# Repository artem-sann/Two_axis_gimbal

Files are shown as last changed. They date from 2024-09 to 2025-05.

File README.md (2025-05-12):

# 📦 Разработка двухосевого подвеса направленной антнны для установки на БПЛА

**Краткое описание:**  
Для достижения значительного увеличения дальности разрабатывается система ретрансляции управляющего сигнала и видеосигнала. Предполагается, что использование дополнительного БПЛА между оператором и FPV летательным аппаратом увеличит дальность полета, при этом уделяется внимание использованию направленных антенн, и их позиционирование при помощи следящего привода, используя как входные данные уровень сигнала - RSSI (Received Signal Strength Indicator). Концепт системы на рис. 1.

<p align="center">
  
</p>

---

## 📁 Структура проекта

```
Two_axis_gimbal/
│
├── 3D_модели/                    # 3D-модели и детали (Inventor)
│   ├── Вспомогательные модели/   # Сборка для предварительных расчетов (Inventor)             
│   ├── Основная сборка/          # Основная сборка
│   └── Испытательный стенд/      # Сборка испытательного стенда
│
├── Dual_BLDC_Controller/         # Проект печатной платы блока управления (Altium)
│   └── Library                   # Собственная библиотека компонентов
│
├── MATLAB_part/                  # Мат. моделирование и синтез корректирующего устройства
│   └── scripts
│       └── Read_COM              # Скрипт для считывания показаний устройства через COM-порт
├── Python/                       # Скрипты визуализации алгоритмов управления
│   └── ...            
│
├── STM32/                        # ПО для микроконтроллера STM32F401
│   └── ...
│
├── Функциональные и кинематические схемы и тд/               
│   └── ...
│
├── Документация/                 # Все НИРы КП и КР и прочая текстовая документация
│   └── ...
│
├── LICENSE               # Лицензия проекта
├── README.md             # Документация первого уровня (этот файл)
└── .gitignore
```

---

## 🛠️ Используемые технологии

- **MCU:** STM32F401
- **CAD:** Компас / SolidWorks / Inventor
- **Программирование:** C, Python, Matlab, Simulink 
- **Протоколы связи и технологии:** UART, SPI, DMA, ADC, PWM
- **Среда разработки:** STM32CubeIDE, VS Code, Matlab
---

## 🖼️ Превью проекта

> Реализованный прототип для тестирования и отработки основного функционала:
<p align="center">
  
</p>

---

## 📃 Документация

Подробная информация доступна в папке `Документация/`. Включает:

- 2 НИРа с общим описанием системы
- КП по ТАУ с описанием системы управления
- КП по Электронике с описанием платы управления
- Календарные планы
- КП по экономике

---

## 🔧 Сборка и запуск

1. **Сборка аппаратной части**  
   Ознакомьтесь с файлами в `3D_модели/`. В ней расположен Inventor проект с подробной 3Д моделью.

2. **Прошивка микроконтроллера**  
   Перейдите в папку `STM32/`, откройте проект в [PlatformIO / STM32CubeIDE] и прошейте контроллер.

---

## 🧪 Тестирование

Результаты тестирования представлены в файле НИР2_оформленный.docx

<p align="center">
  
  
</p>

---

## 🤝 Участие

Если вы хотите внести вклад:

1. Сделайте форк проекта
2. Создайте ветку для своей функции (`git checkout -b feature/YourFeature`)
3. Сделайте коммит (`git commit -m 'Add some feature'`)
4. Отправьте пул-реквест

---

## 📬 Контакты

- Автор: [Артём Санников]
- Email: [artemksannikov@gmail.com]
- Telegram: [@artem_sann]

---

## 📌 TODO

- [ ] Привести код для STM32 в порядок
- [ ] Переработать печатную плату с учетом правок
- [ ] Опубликовать где нибудь

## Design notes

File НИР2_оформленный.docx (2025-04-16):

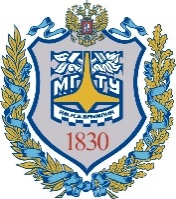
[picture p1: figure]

| Министерство науки и высшего образования Российской Федерации Федеральное государственное бюджетное образовательное учреждение высшего образования «Московский государственный технический университет имени Н.Э. Баумана (национальный исследовательский университет)» (МГТУ им. Н.Э. Баумана)

ФАКУЛЬТЕТ «Специальное машиностроение»

КАФЕДРА «Робототехнические системы и мехатроника»

РАСЧЕТНО-ПОЯСНИТЕЛЬНАЯ ЗАПИСКА

К НАУЧНО-ИССЛЕДОВАТЕЛЬСКОЙ РАБОТЕ

НА ТЕМУ:

Разработка двухосевого привода направленной антенны для установки на БПЛА

Студент СМ7-82Б _________________ Санников А.К.

(Группа) (Подпись, дата) (И.О.Фамилия)

Руководитель _________________ Гуляев И.А.

(Подпись, дата) (И.О.Фамилия)

Консультант _________________ ____________________

(Подпись, дата) (И.О.Фамилия)

2025 г.

Министерство науки и высшего образования Российской Федерации

Федеральное государственное бюджетное образовательное учреждение

высшего образования

«Московский государственный технический университет имени Н.Э. Баумана

(национальный исследовательский университет)»

(МГТУ им. Н.Э. Баумана)

УТВЕРЖДАЮ

Заведующий кафедрой __________

(Индекс)

______________ _______________

(И.О.Фамилия)

« _____ » ____________ 20 ____ г.

ЗАДАНИЕ

на выполнение научно-исследовательской работы

По теме: | Разработка двухосевого привода направленной антенны

для установки на БПЛА

Студент группы ____СМ7-82б___________

_________________________Санников Артём Константинович__________________________

(Фамилия, имя, отчество)

Направленность НИР (учебная, исследовательская, практическая, производственная, др.)

________практическая____________________________________________________________

Источник тематики (кафедра, предприятие, НИР) _____________________________________

График выполнения НИР: 25% к 5 нед., 50% к 7 нед., 75% к 10 нед., 100% к 12 нед.

Техническое задание | Разработать двухосевой привод для встраивания в систему

ретрансляции сигнала с возможностью установки на БПЛА для увеличения дальности

передачи сигнала

Оформление научно-исследовательской работы:

Расчетно-пояснительная записка на _____ листах формата А4.

Перечень графического (иллюстративного) материала (чертежи, плакаты, слайды и т.п.)

_______________________________________________________________________________

_______________________________________________________________________________

_______________________________________________________________________________

Дата выдачи задания « 17 » февраля 2025 г.

Руководитель НИР _________________ Гуляев И.А.

(Подпись, дата) (И.О.Фамилия)

Студент _________________ Санников А.К.

(Подпись, дата) (И.О.Фамилия)

Примечание: Задание оформляется в двух экземплярах: один выдается студенту, второй хранится на кафедре.

# РЕФЕРАТ

Расчетно-пояснительная записка 27 с. 17 рис., 3 табл., 8 источников.

ДВУХОСЕВОЙ ПРИВОД, БПЛА, НАПРАВЛЕННЫЕ АНТЕННЫ, РЕТРАНСЛЯТОР, РАЗРАБОТКА ПРИВОДА, РАЗРАБОТКА ПРОТОТИПА.

Объектом разработки является двухосевой привод направленной антенны.

Цель работы – разработка части системы ретрансляции сигнала для установки на БПЛА для увеличения дальности передачи сигнала, в частности прототип и испытательный стенд, а также систему управления.

Поставленная цель достигается за счет разработки двухосевого привода, направляющего антенну ретранслятора с необходимой точностью и с необходимым быстродействием, и установки данной системы на дополнительный БПЛА.

СОДЕРЖАНИЕ

# ВВЕДЕНИЕ

В настоящее время все чаще используются беспилотные летательные аппараты с FPV системами, как в исследовательских и разведывательных целях, так и в боевых условиях. Всё чаще возникает потребность в увеличении дальности работы, но при этом остается условие сохранять высокие скорости передачи данных. Решение задачи увеличения дальности передачи сигнала возможно за счёт установки ретранслятора с усилителем и на управляемом подвесе на вспомогательный БПЛА.

# 1 ОПИСАНИЕ СИСТЕМЫ И ПОСТАНОВКА ЗАДАЧИ

Для достижения значительного увеличения дальности разрабатывается система ретрансляции управляющего сигнала и видеосигнала. Предполагается, что использование дополнительного БПЛА между оператором и FPV летательным аппаратом увеличит дальность полета, при этом уделяется внимание использованию направленных антенн, и их позиционирование при помощи следящего привода, используя как входные данные уровень сигнала - RSSI (Received Signal Strength Indicator). Концепт системы на рис. 1.

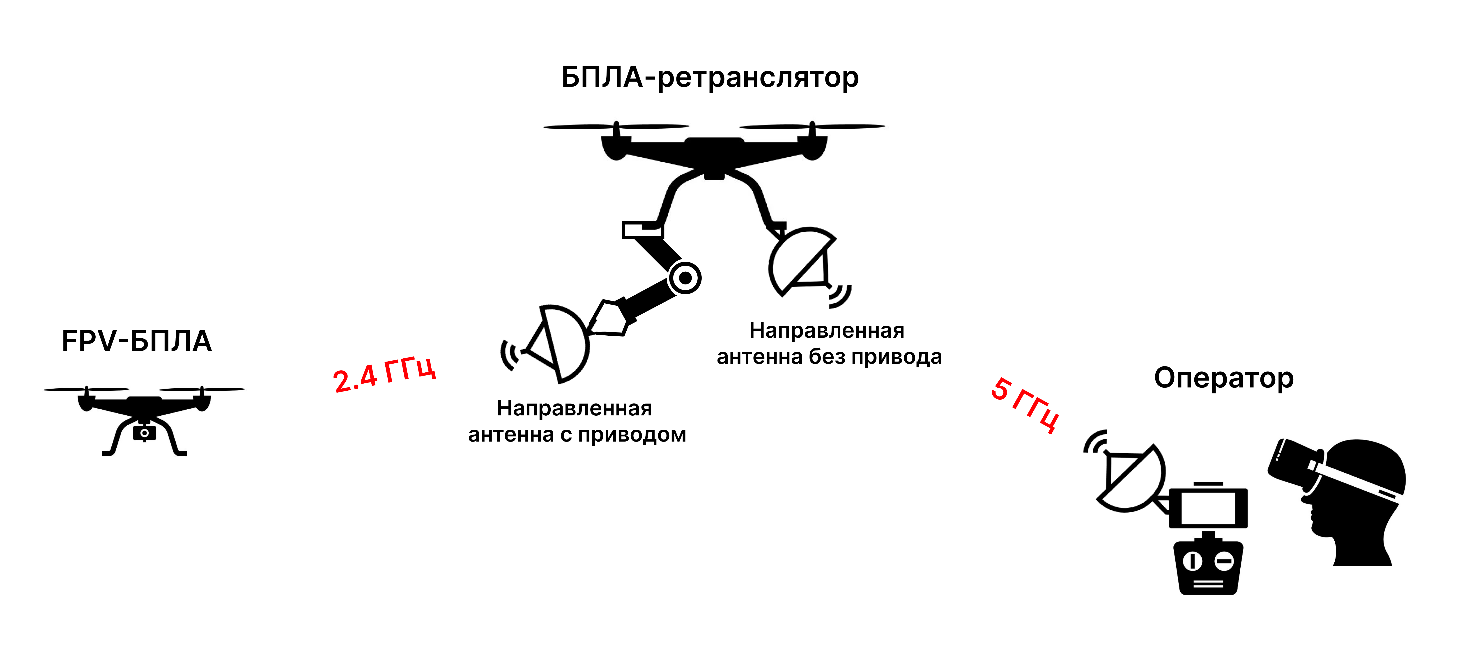
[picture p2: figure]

Рис. 1 Концепт системы ретрансляции

При этом на дрон ретранслятор устанавливается 2 антенны, одна из которых остается неподвижной и направляется при помощи поворота дрона, а вторая устанавливается на двухосевой привод, который в свою очередь направляет антенну на FPV-дрон.

В рамках данного проекта ставится техническое задание на разработку только части системы – двухосевого привода антенны, и выбор компонетов системы: антенн и тд.

# 2 КОНСТРУКЦИЯ РАЗРАБАТЫВАЕМОГО ИЗДЕЛИЯ

Разрабатываемое устройство представляет из себя – подвесной модуль для мультикоптерных
Здесь кинематическая схема

## 2.1 Разработка прототипа

Данная система позволяет увеличивать дальность полетов, что будет очень полезно для применения в боевых условиях, а также для разведывательных и исследовательских целей, везде где требуется большая дальность и сохранение FPV функций.

## 2.2 Разработка испытательного стенда

Существуют двухосевые подвесы-стабилизаторы для аэрофотосъемки, также существуют дроны-ретрансляторы с двумя неподвижными антеннами широкой направленности. По сути новизна заключается в объединении этих двух идей, с целью увеличения дальности полета и повышении эффективности ретрансляции.

Основная актуальность работы – применение в боевых условиях. Так как в таких условиях наиболее важна дальность передачи сигнала.

# 3 ИЗГОТОВЛЕНИЕ И СБОРКА ПРОТОТИПА И ИСПЫТАНИЯ

## 3.1 Изготовление деталей

Рассматривая аналоги привода можно рассмотреть как косвенные аналоги – подвесы-

## 3.2 Сборка и подключение стенда

По контекстным запросам:

- «Разработка двухосевого привода направленной антенны для установки на БПЛА»
- «two-axis drive of directional antenna for UAV. UAV is equipped with device with 2-axis drive and directional antenna, using stepper motors directs antenna.»,
- « двухосевой привод направленной антенны для бпла с для увеличения дальности полетов на бпла устанавливается устройство с 2 осевым приводом, и направленной антенной, с помощью шаговых двигателей направляет антенну.»

Отсутствуют релевантные результаты.

## 3.3 Реализация корректирующего устройства на МК и испытания

# 4 ОПРЕДЕЛЕНИЕ ПРИГОДНЫХ ТИПОВ И РАЗМЕРОВ БПЛА

грузоподъемности представлена в таблице 1:

Таблица 1. Сравнение типов и размеров БПЛА

Типоразмер БПЛА | Масса | Грузо-сть | Габариты в диаметр | Время полета | Макс.Высота полета
Микро-класс | До 50 гр. | 10 гр. | До 100 мм | 3-10 мин. | 10 м
Мини-класс | До 500 гр. | 100 гр. | До 250 мм. | 5-20 мин. | 100 м
Средний класс | До 2.5 кг. | 500 гр. | 350-500 мм | 30 мин. | 1000 м
Тяжелый класс | От 2.5 кг. | От 1 кг. | От 550 мм | От 50 мин. | От 1000 м

Для прототипа предприятием заказчиком был выбран квадрокоптер тяжелого класса: DJI MATRICE 300, его характеристики можно брать за основу при проектировании привода, внешний вид представлен на рис. 5.

# 4 УРАВНЕНИЯ ДВИЖЕНИЯ И РАСЧЕТ РАБОЧЕЙ ОБЛАСТИ УСТРОЙСТВА

Для определения структуры устройства создадим функциональную схему. В данной научно-исследовательской работе рассматривается разработка одной из частей системы – часть на рис. 6 начиная с микроконтроллера и ниже.

Рис. 6 Функциональная схема устройства

# ЗАКЛЮЧЕНИЕ

В заключение работы, обобщим краткое техническое задание на разработку двухосевого привода.

# СПИСОК ИСПОЛЬЗОВАННЫХ ИСТОЧНИКОВ

1) Ротхаммель К. Энциклопедия антенн: Antennenbuch под ред. Кришке А. Изд. 11-е: Издательство ДМК-Пресс 2016. 812с. ISBN 978-5-97060-217-1

2) Биард Рэндал У., МакЛэйн Тимоти У. Малые беспилотные летательные аппараты: теория и практика 2012. 309 с.

3) C.В. Овсянников, А.А. Бошляков, А.О. Кузьмина ЭКСПЕРИМЕНТАЛЬНЫЕ ИССЛЕДОВАНИЯ В МЕХАТРОННЫХ СИСТЕМАХ

4) DJI LLC Краткое руководство пользователя DJI MATRICE 300 2015. 109 с.

5) Кокорев Ю.А., Жаров В.А., Торгов А.М. Расчет электромеханического привода: Учеб. пособие Под ред. В.Н.Баранова. — М.: Изд-во МГТУ, І995. 132 с

6) А.И. Еремеев и др.; Под. ред. О.Ф. Тищенко. А 1. тлас конструкций элементов приборных устройств: Учеб. Пособие для студентов приборостроительных специальностей ВУЗов /А.А. Буцев, М.: Машиностроение, 1982. 116с.

7) М. Г. Алешин, С. В. Дьяконов, А. Ю. Сивов, ОБОСНОВАНИЕ ОСНОВНЫХ ХАРАКТЕРИСТИК АНТЕННОЙ СИСТЕМЫ И ПАРАМЕТРОВ УПРАВЛЕНИЯ МОЩНОСТЬЮ ПЕРЕДАТЧИКА РЕТРАНСЛЯТОРА СВЯЗИ НА БЕСПИЛОТНОМ ЛЕТАТЕЛЬНОМ АППАРАТЕ 2011. 21 c.

8) К.О. Коровин , С.В. Кузьмин, Реализация канала связи с БПЛА с использованием широкополосных малоэлементных антенных решеток в качестве бортовых антенных систем, 2020, 6 с.

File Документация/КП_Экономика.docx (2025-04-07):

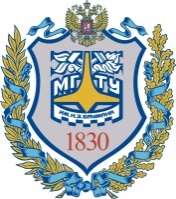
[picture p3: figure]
Gerb-BMSTU_01

| Министерство образования и науки Российской Федерации Федеральное государственное бюджетное образовательное учреждение высшего образования «Московский государственный технический университет имени Н.Э. Баумана (национальный исследовательский университет)» (МГТУ им. Н.Э. Баумана)

ФАКУЛЬТЕТ ИНЖЕНЕРНЫЙ БИЗНЕС И МЕНЕДЖМЕНТ

КАФЕДРА ЭКОНОМИКА И ОРГАНИЗАЦИЯ ПРОИЗВОДСТВА

РАСЧЕТНО-ПОЯСНИТЕЛЬНАЯ ЗАПИСКА

К КУРСОВОЙ РАБОТЕ ПО КУРСУ

ЭКОНОМИКА ПРЕДПРИЯТИЯ

НА ТЕМУ:

Организация и планирование

проведения НИОКР по теме

«Разработка двухосевого _

_ привода направленной антенны ___ _ _ для установки на БПЛА» __

Студент ____СМ7-82Б__ _________________ _Санников А .К__

(Группа) (Подпись, дата) (И.О.Фамилия)

Руководитель курсовой работы _________________ ___А.В.Волохов _

(Подпись, дата) (И.О.Фамилия)

Москва 2025 г.

# 1. Введение

В настоящее время все чаще используются беспилотные летательные аппараты с FPV системами, как в исследовательских и разведывательных целях, так и в боевых условиях. Всё чаще возникает потребность в увеличении дальности работы, но при этом остается условие сохранять высокие скорости передачи данных. Решение задачи увеличения дальности передачи сигнала возможно за счёт установки ретранслятора с усилителем и на управляемом подвесе на вспомогательный БПЛА.

Для достижения значительного увеличения дальности разрабатывается система ретрансляции управляющего сигнала и видеосигнала. Предполагается, что использование дополнительного БПЛА между оператором и FPV летательным аппаратом увеличит дальность полета, при этом уделяется внимание использованию направленных антенн, и их позиционирование при помощи следящего привода, используя как входные данные уровень сигнала - RSSI (Received Signal Strength Indicator). Концепт системы на рис. 1.


Рис. 1 Концепт системы ретрансляции

При этом на дрон ретранслятор устанавливается 2 антенны, одна из которых остается неподвижной и направляется при помощи поворота дрона, а вторая устанавливается на двухосевой привод, который в свою очередь направляет антенну на FPV-дрон.

Для этого необходимо разработать систему управления приводом (рис. 2) и отдельную плату, для управления электроприводами (рис. 3).

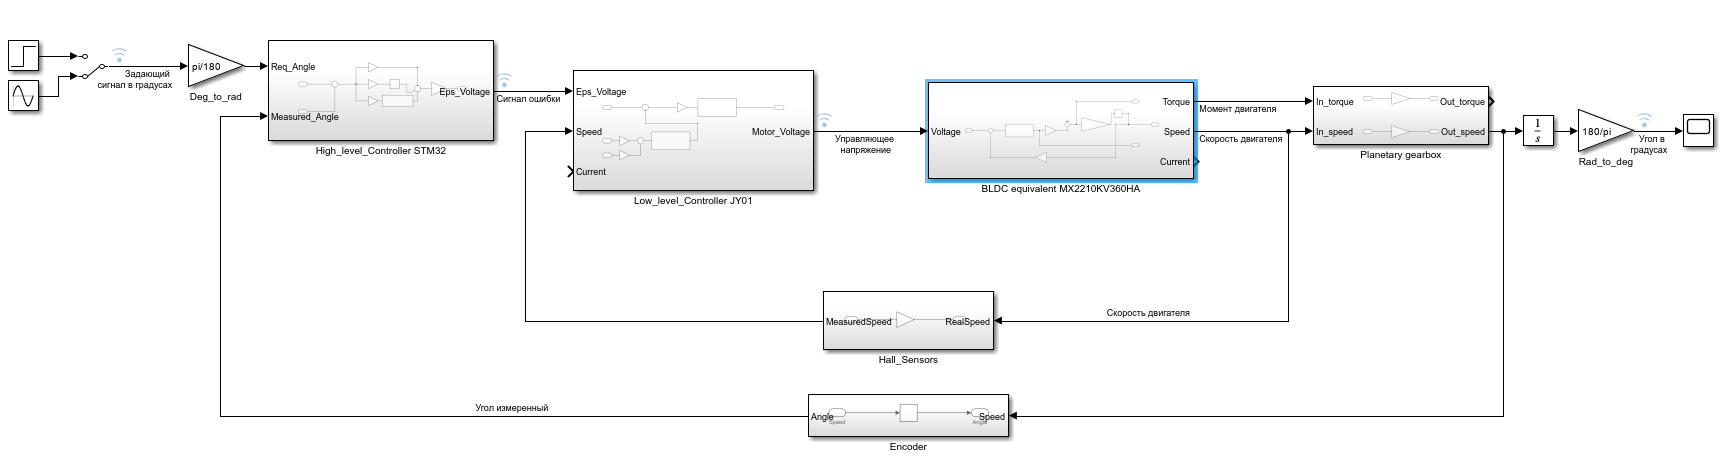
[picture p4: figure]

Рис. 2– система управления приводом

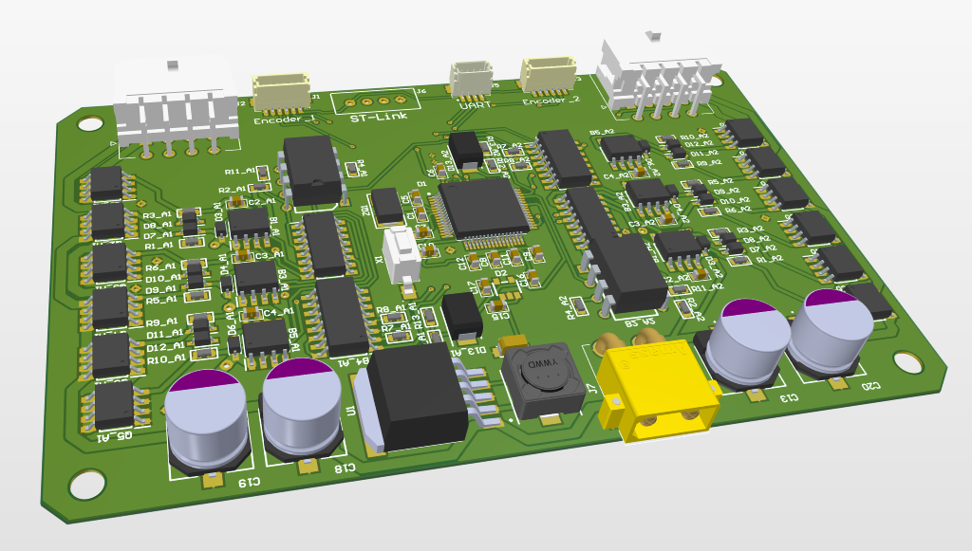
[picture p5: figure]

Рис. 3– плата системы управления приводом

В рамках данной курсовой работы будет рассмотрена организация научно-исследовательской и опытно-конструкторской работы. Для этого необходимо:

1. Разбить проект на отдельные части.
2. Определить длительность каждого этапа проектирования и производства.
3. Выбрать необходимое оборудование и работников для производства изделия.
4. Далее, после проведения всех расчетов, произвести оценку технической и экономической составляющих НИОКР.
5. Проанализировать все составляющие и сделать вывод о возможности производства данного изделия.

# 2. Основная часть

Составим дифференциальный перечень работ по всем этапам НИОКР с учётом их специфики:

Перечень этапов НИР:

- разработка технического задания на НИР;
- выбор направления исследования;
- подготовка экспериментальной базы;
- теоретические и экспериментальные исследования;
- обобщение и оценка результатов исследований;

Перечень этапов ОКР:

- разработка технического задания на ОКР;
- разработка технического предложения;
- эскизное проектирование;
- техническое проектирование;
- разработка рабочего проекта и оформление технической документации;
- изготовление опытного образца;
- испытания опытного образца;
- доработка проекта по результатам испытаний.

## 2.1. Определение сроков проведения НИОКР с составлением план-графика

Для определения сроков проведения НИОКР используем вероятностную методику определения продолжительности проведения работ на основе двухточечной оценки трудоёмкости:

T_(ож i) =(3T_(mini) +2T_(maxi))/5

Где:

T_(ож i) - ожидаемая продолжительность проведения работ;

T_(mini) – минимальная продолжительность проведения работы;

T_(maxi) – максимальная продолжительность проведения работы.

T_i =(τ_i k_(р-к))/(R_i F_(пл) K_(вн))

Где:

T_i – продолжительность проведения работы i при использовании трудоёмкости;

τ_i – трудоёмкость работы i (чел.-дн.);

k_(р-к) =1,45 – коэффициент перевода рабочих дней в календарные (если F_(пл) задан в календарных днях за период);

R_i – число исполнителей работы i, чел.;

F_(пл) – плановый фонд рабочего времени исполнителя за период в рабочих/календарных днях за рассматриваемый календарный период;

K_(вн) =1 – коэффициент выполнения норм.

## 2.2. Определение продолжительности разработки технического задания на НИР

Для составления технического задания требуется работа одного инженера 1-й категории. Ему следует:

- изучить техническую литературу по тематике (порядка 200-300 страниц);
- изучить патенты и результаты смежных исследований (порядка 100 страниц);
- на основе изученной литературы, целей и задач разработки – составить техническое задание.
- Изучить ранее полученные наработки

Таким образом объём работ на данном этапе состоит из изучения 450 страниц технической литературы и формулирования ТЗ на основе полученных данных.

Из расчёта изучения страницы текста с использованием полученных из неё сведений для составления ТЗ за 0,25 часа потребуется: 450*0,25=112 часов непрерывной работы.

Минимальная продолжительность работы выйдет при 8-ми часовом рабочем дне и отсутствии перерывов: 8/(0,25)=32 проработанные страницы в день.

τ_(min1) =400/32=12,5=13 дней

Максимальная продолжительность работы выйдет при наличии длительных перерывов и незапланированных задержек в течение рабочего дня. С учётом вышеперечисленного примем количество проработанных за день страниц равным 15.

τ_(max1) =300/15=20 дней

k_(р-к) =1,45 ;

R_1 =1 ;

F_(пл) =1;

K_(вн) =1 .

T_(min1) =(τ_(min1) k_(р-к))/(R_1 F_(пл) K_(вн))=(13*1,45)/(1*1*1)=18,85=19

T_(max1) =(τ_(max1) k_(р-к))/(R_1 F_(пл) K_(вн))=(20*1,45)/(1*1*1)=29

T_(ож 1) =(3T_(min1) +2T_(max1))/5=(3*19+2*29)/5=23

Получаем 23 рабочих дня.

## 2.3. Определение продолжительности выбора направления исследования

Для выбора направления исследования требуется работа одного инженера 2-й категории. Ему следует:

- проанализировать требования к ТЗ на основе технической литературы по тематике НИР (порядка 50 страниц);
- изучить принципы работы ближайших аналогов на основе технической документации и обзорной технической литературы (порядка 200 страниц);
- сформулировать основные принципы выбранного направления исследования.

Тогда объём работ на данном этапе состоит из изучения 250 страниц технической литературы и формулирования выбранного направления исследований.

Из расчёта проведения анализа страницы текста для выбора направления исследования за 0,25 часа, потребуется: 250*0,25=62.5 часов непрерывной работы минимум.

Минимальная продолжительность работы выйдет при 8-ми часовом рабочем дне и отсутствии перерывов: 8/(0,25)=32 проработанных страниц в день.

τ_(min2) =250/32=7.8125=8 дней

Максимальная продолжительность работы выйдет при наличии длительных перерывов и незапланированных задержек в течение рабочего дня. С учётом вышеперечисленного примем количество проработанных за день страниц равным 15.

τ_(max2) =250/15=16.67=17 дней

k_(р-к) =1,45 ;

R_2 =1 ;

F_(пл) =1;

K_(вн) =1 .

T_(min2) =(τ_(min2) k_(р-к))/(R_1 F_(пл) K_(вн))=(8*1,45)/(1*1*1)=11,6=12

T_(max2) =(τ_(max2) k_(р-к))/(R_2 F_(пл) K_(вн))=(17*1,45)/(1*1*1)=24.65=25

T_(ож 2) =(3T_(min2) +2T_(max2))/5=(3*12+2*25)/5=17.2=18 дней

Получаем 18 рабочих дней.

## 2.4. Определение продолжительности подготовки экспериментальной базы

Для подготовки экспериментальной базы требуется 3 рабочих – наладчик сборщик-паяльщик, программист 2-го разряда:

- приобрести и подготовить к работе стенды наладки (один наладчик);
- организовать условия для испытаний, приобрести необходимые компоненты и инструменты для сборки модели (один сборщик-паяльщик);
- собрать модель для испытания (один сборщик-паяльщик);
- приобрести компьютер и установить программное обеспечение для программирования микроконтроллеров (один программист 2-го разряда).

Расчёт продолжительности этапа проведём по наиболее длительному из происходящих процессов – приобретение необходимых компонентов и инструментов для сборки модели, для сборки макета и подготовки испытаний.

Такой процесс может занять от одного до 40 рабочих дней (8 недель) рабочих дней в зависимости от наличия компонентов.

T_(min3) ^(') =1 дня

T_(max3) ^(') =40 дней

Процесс сборки охватывает демонтаж и монтаж порядка 150 единиц электрических и механических компонентов. Из расчёта монтажа компонента средней сложности за 0,5 часа потребуется: 150*0,5=100 часов непрерывной работы.

Минимальная продолжительность работы выйдет при 8-ми часовом рабочем дне и отсутствии перерывов: 8/(0,5)=16 монтированных компонентов в день.

τ_(min3) =150/16=9,375=10 дней

В худшем же случае положим множество перерывов в течение рабочего дня, повышенную сложность проведения конкретной операции монтажа и незапланированные задержки, примем количество монтированных за день компонентов равным 8.

Тогда:

τ_(max3) =150/8=18.75=19 ;

k_(р-к) =1,45 ;

R_3 =5 ;

F_(пл) =1;

K_(вн) =1 .

T_(min3) =T_(min3) ^(') +(τ_(min3) k_(р-к))/(R_3 F_(пл) K_(вн))=1+(10*1,45)/(5*1*1)=3.9=4

T_(max3) =T_(max3) ^(') +(τ_(max3) k_(р-к))/(R_3 F_(пл) K_(вн))=40+(19*1,45)/(5*1*1)=45,51=46

T_(ож 3) =(3T_(min3) +2T_(max3))/5=(3*4+2*46)/5=20,8=21

Получаем 21 рабочих дней.

## 2.5. Определение продолжительности теоретических и экспериментальных исследований

Для проведения теоретических и экспериментальных исследований требуется совместная работа двух инженеров 3-й категории. Им следует:

- проанализировать стендовые испытания модели (порядка 20 часов);
- провести испытания на подготовленной модели (порядка 40 часов);
- в ходе испытаний проводить текущую наладку модели (порядка 10 часов).

Итого, объём работ на данном этапе предполагает затраты около 70 часов. В минимальном случае при 8-ми часовом рабочем дне получим: 8 часов испытаний в день.

τ_(min4) =70/8=8.75=9 ;

В худшем же случае положим множество перерывов в течение рабочего дня и незапланированные задержки, примем количество проведённых за испытаниями часов в день равным 4.

Тогда:

τ_(max4) =70/4=17.5=18 ;

k_(р-к) =1,45 ;

R_4 =2 ;

F_(пл) =1;

K_(вн) =1 .

T_(min4) =(τ_(min4) k_(р-к))/(R_4 F_(пл) K_(вн))=(9*1,45)/(2*1*1)=6,53=7

T_(max4) =(τ_(max4) k_(р-к))/(R_4 F_(пл) K_(вн))=(18*1,45)/(2*1*1)=13,05=14

T_(ож 4) =(3T_(min4) +2T_(max4))/5=(3*7+2*14)/5=9,8=10

Получаем 10 рабочих дней.

## 2.6. Определение продолжительности обобщения результатов исследований

Для обобщения результатов исследований требуется работа одного инженера 2-й категории. Ему следует:

- проанализировать заявленные цели и задачи, а также утверждённое ТЗ (порядка 15 страниц);
- проанализировать результаты исследований (порядка 30 страниц);
- создать отчёт по результатам проведённых исследований, сделать выводы и дать рекомендации по дальнейшему развитию проекта (порядка 30 страниц).

Объём работ на данном этапе состоит из анализа 45 страниц и написания 30 страниц технической литературы с формированием выводов на её основе. В сумме необходимо обработать 75 страниц.

Из расчёта проведения анализа страницы ТЗ и результата исследования для обобщения информации за 1.5 час, потребуется: 75*1.5=112.5 часов непрерывной работы.

Минимальная продолжительность работы выйдет при 8-ми часовом рабочем дне и отсутствии перерывов: 8/1=8 проработанных страниц в день.

τ_(min5) =112.5/8=14.0625=15 дней

Максимальная продолжительность работы выйдет при наличии длительных перерывов и незапланированных задержек в течение рабочего дня. С учётом вышеперечисленного примем количество проработанных за день страниц равным 4.

τ_(max5) =112.5/4=28.125=29 дней

k_(р-к) =1,45 ;

R_5 =1 ;

F_(пл) =1;

K_(вн) =1 .

T_(min5) =(τ_(min5) k_(р-к))/(R_5 F_(пл) K_(вн))=(15*1,45)/(1*1*1)=21.75=22

T_(max5) =(τ_(max5) k_(р-к))/(R_5 F_(пл) K_(вн))=(29*1,45)/(1*1*1)=42,05=43

T_(ож 5) =(3T_(min5) +2T_(max5))/5=(3*22+2*43)/5=30.4

Получаем 31 рабочих дней.

## 2.7. Определение продолжительности разработки технического задания на ОКР разработки технического предложения и эскизного проекта

Для составления технического задания требуется работа одного инженера 2-й категории. Ему следует:

- изучить техническую литературу по тематике (порядка 300 страниц);
- изучить результаты патентных исследований по смежным тематикам (порядка 100 страниц);
- изучить документацию и результаты НИР (порядка 30 страниц)
- на основе изученной литературы и поставленных целей и задач разработки – составить техническое задание.

Итого, объём работ на данном этапе состоит из изучения 430 страниц технической литературы и формулирования ТЗ на основе полученных данных.

Из расчёта изучения страницы текста с использованием полученных из неё сведений для составления ТЗ за 0,25 часа, потребуется: 430*0,25=107.5 часов непрерывной работы. Таким образом, в минимальном случае при 8-ми часовом рабочем дне получим: 8/(0,25)=32 проработанных страниц в день. В худшем же случае положим множество перерывов в течение рабочего дня и незапланированные задержки, примем количество проработанных за день страниц равным 16.

Тогда:

τ_(min6) =430/32=13,4375=14 ;

τ_(max6) =430/16=26,875=27 ;

k_(р-к) =1,45 ;

R_6 =1 ;

F_(пл) =1;

K_(вн) =1 .

T_(min6) =(τ_(min6) k_(р-к))/(R_6 F_(пл) K_(вн))=(14*1,45)/(1*1*1)=20,3=21

T_(max6) =(τ_(max6) k_(р-к))/(R_6 F_(пл) K_(вн))=(27*1,45)/(1*1*1)=39,15=40

T_(ож 6) =(3T_(min6) +2T_(max6))/5=(3*21+2*40)/5=28,6=29

Получаем 29 рабочих дней.

## 2.8. Определение продолжительности технического проектирования

Для технического проектирования требуется работа одного инженера 2-й категории. Ему следует:

- создать технический проект и 3Д-модель с использованием САПР (порядка 20-40 часов);

τ_(min9) =20/8=2,5=3 дня

τ_(max9) =40/4=10 дней

- осуществить нормоконтроль ( +10…20%) .

Создание технического проекта требует примерно столько же времени, сколько и создание эскизного проекта.

Тогда объём работ на данном этапе состоит из выполнения проектирования в САПР и нормоконтроля.

T_(ож 9) =T_(ож 8) (100%+20%)=5*120%=6

Получаем 6 рабочих дней.

## 2.9. Определение продолжительности разработки рабочего проекта и оформления технической документации

Для разработки рабочего проекта и оформления технической документации требуется работа одного инженера 3-й категории. Ему следует:

- на основе предыдущих работ подготовить рабочий проект (порядка 20 часов);
- оформить конструкторскую документацию с учётом актуальных требований ГОСТ (порядка 80 часов).

Итого, объём работ на данном этапе предполагает затраты около 100 часов. В минимальном случае при 8-ми часовом рабочем дне получим: 8 часов работы в день. В худшем же случае положим множество перерывов в течение рабочего дня и незапланированные задержки, примем количество проведённых за работой часов равным 4.

Тогда:

τ_(min10) =100/8=12.5=13 ;

τ_(max10) =100/4=25 ;

k_(р-к) =1,45 ;

R_10 =1 ;

F_(пл) =1;

K_(вн) =1 .

T_(min10) =(τ_(min10) k_(р-к))/(R_10 F_(пл) K_(вн))=(13*1,45)/(1*1*1)=18,85=19

T_(max10) =(τ_(max10) k_(р-к))/(R_10 F_(пл) K_(вн))=(25*1,45)/(1*1*1)=36,25=37

T_(ож 10) =(3T_(min10) +2T_(max10))/5=(3*19+2*37)/5=26,2=27

Получаем 27 рабочий день.

## 2.10. Определение продолжительности изготовления опытного образца

Для изготовления опытного проекта требуется совместная работа одного паяльщика-сборщика. Им следует:

- руководствуясь технической документацией, изготовить опытный образец (порядка 60 часов);
- кратко проверить образец на работоспособность (порядка 10 часов).

Итого, объём работ на данном этапе предполагает затраты около 70 часов. В минимальном случае при 8-ми часовом рабочем дне получим: 8 часов работы или испытаний в день. В худшем случае примем количество проведённых за работой или испытаниями часов равным 4.

Тогда:

τ_(min11) =70/8=8,75=9 ;

τ_(max11) =70/4=17,5=18 ;

k_(р-к) =1,45 ;

R_11 =2 ;

F_(пл) =1;

K_(вн) =1 .

T_(min11) =(τ_(min11) k_(р-к))/(R_11 F_(пл) K_(вн))=(9*1,45)/(2*1*1)=6,525=7

T_(max11) =(τ_(max11) k_(р-к))/(R_11 F_(пл) K_(вн))=(18*1,45)/(2*1*1)=13,05=14

T_(ож 11) =(3T_(min11) +2T_(max11))/5=(3*7+2*14)/5=9,8=10

Получаем 10 рабочих дней.

## 2.11. Определение продолжительности испытаний опытного образца

Для проведения испытаний опытного образца требуется совместная работа двух инженеров 3-й категории. Им следует:

- проанализировать стендовые испытания образца (порядка 20 часов);
- провести испытания на подготовленном макете (порядка 80 часов);
- провести испытания на выносливость (порядка 60 часов);
- провести испытания степени защиты (порядка 40 часов)
- в ходе испытаний проводить текущую наладку модели (порядка 20 часов).

Итого, объём работ на данном этапе предполагает затраты около 110 часов. В минимальном случае при 8-ми часовом рабочем дне получим: 8 часов испытаний в день. В худшем же случае положим множество перерывов в течение рабочего дня и незапланированные задержки, примем количество проведённых за день испытаний равным 4.

Тогда:

τ_(min12) =220/8=27.5=14 ;

τ_(max12) =220/4=28 ;

k_(р-к) =1,45 ;

R_12 =2 ;

F_(пл) =1;

K_(вн) =1 .

T_(min12) =(τ_(min12) k_(р-к))/(R_12 F_(пл) K_(вн))=(14*1,45)/(2*1*1)=10.9=11

T_(max12) =(τ_(max12) k_(р-к))/(R_12 F_(пл) K_(вн))=(28*1,45)/(2*1*1)=19.875=20

T_(ож 12) =(3T_(min12) +2T_(max12))/5=(3*11+2*20)/5=14,6=15

Получаем 15 рабочих дней.

## 2.12. Определение продолжительности доработки проекта по результатам испытаний опытного образца

Для проведения доработки проекта по результатам испытаний опытного образца требуется совместная работа двух инженеров 3-й категории. Им следует:

- проанализировать результаты испытаний опытного образца (порядка 10 часов);
- доработать опытный образец (порядка 30 часов);
- провести испытания, подтверждающие эффективность доработки (порядка 10 часов).

Объём работ на данном этапе составляет около 50 часов.

Минимальная продолжительность работы выйдет при 8-ми часовом рабочем дне и отсутствии перерывов: 8 часов работы в день.

τ_(min13) =50/8=6.25=7 дней

## 2.13. Результаты расчетов продолжительности исполнения работ НИОКР

Итог расчётов продолжительности исполнения работ НИОКР подведён в таблице 1.

Таблица 1. Результаты расчетов продолжительности работ.

Этапы | Тип исполнителей | Количество исполнителей | Трудоёмкость работ, дней | | Продолжительность работ, рабочих дней
| | | τ_(min) | τ_(max)
1 | Инженер 1-й категории | 1 | 19 | 29 | 23
2 | Инженер 2-й категории | 1 | 12 | 25 | 18
3 | Наладчик | 1 | 4 | 46 | 21
| Паяльщик-сборщик | 1
| Программист 2-го разряда | 1
4 | Инженер 3-й категории | 2 | 7 | 14 | 10
5 | Инженер 2-й категории | 1 | 22 | 43 | 31
6 | Инженер 2-й категории | 1 | 21 | 40 | 29
9 | Инженер 2-й категории | 1 | 3 | 10 | 6
10 | Инженер 3-й категории | 1 | 19 | 37 | 27
11 | Сборщик-паяльщик | 1 | 7 | 14 | 10
| Программист 2-го разряда | 1
12 | Инженер 3-й категории | 2 | 21 | 40 | 29
13 | Инженер 3-й категории | 2 | 10 | 19 | 14

На основании рассчитанной продолжительности этапов и работ был построен ленточный график выполнения НИОКР (см. приложение А)

# 3. Расчет стоимости проведения НИОКР

## 3.1. Затраты на оплату труда работников, непосредственно занятых в НИОКР

Оплата труда работников складывается из основной заработной платы, дополнительной заработной платы, включающей премии, стимулирующие и компенсационные выплаты, и отчислений на социальные нужды. [1]

Основная заработная плата определяется ставкой работника и продолжительностью его работы.

Дополнительная заработная плата берётся в размере 20 % от основной.

Отчисления на социальные нужды складываются из отчислений в пенсионный фонд, в фонд социального страхования и медицинского страхования. Нормативы отчислений устанавливаются законодательством [2]:

- Пенсионный фонд – 22 % от основной заработной платы;
- Фонд социального страхования – 2,9 % от основной заработной платы;
- Фонд медицинского страхования – 5,1 % от основной заработной платы.

Таблица с рассчитанными затратами на плату труда работников, непосредственно занятых в НИОКР представлена в приложении Б.

Суммарные затраты составляют: 3 547 799 руб.

## 3.2 Затраты на накладные расходы

Накладные расходы включают оплату аренды помещений, коммунальные расходы, расходы на интернет и сотовую связь. Они принимаются равными 150 % от основной заработной платы работников:

3 547 799 ∙150%=5 321 698,5 рублей

## 3.3 Затраты на материальные ресурсы

Затраты на материальные ресурсы включают в себя основные и косвенные затраты.

Основные затраты – затраты на материалы, покупные изделия и полуфабрикаты, использующиеся непосредственно в НИОКР.

Косвенные затраты – затраты на материалы и оборудование, использующиеся не только в данном НИОКР, их величина рассчитывается через амортизацию этого оборудования.

Величина амортизационных отчислений рассчитывается исходя из длительности эксплуатации оборудования при выполнении НИОКР:

З_(об) =А_(об) ∙(Т_(об))/(Т_(об ∑))

где А_(об) - величина амортизационных отчислений за период;

Т_(об) - время использования оборудования в НИОКР;

Т_(об ∑) - время использования оборудования за период.

Величина амортизационных отчислений за период рассчитывается исходя из стоимости оборудования:

А_(об) =С∙k_a

где С- стоимость оборудования;

k_a - норма амортизационных отчислений за период в долях, устанавливается государством.

В таблице 2 представлены основные затраты на материальные ресурсы, в таблице 3 – косвенные.

Таблица 2. Основные затраты на материальные ресурсы

Наименование | Стоимость единицы, руб. | Количество | Величина затрат, руб.
Микроконтроллер STM32F401RET6 | 600 | 1 | 600
Датчик угла поворота AS5048B | 1480 | 2 | 2960
Двигатель с редкутором BLDC 3626 | 2800 | 2 | 5600
Элементы платы | 15000 | 1 | 15000
Соединительные и корпусные изделия | 1000 | 4 | 4000
Пластик для 3д печати | 1200 | 1 | 1200
Канцелярские принадлежности | 500 | 10 | 5000
Итого | 34 360,00 ₽

Таблица 3. Косвенные затраты на материальные ресурсы

Наименование | Стоимость, руб. | Количество | Время использования | ka%, в месяц | Затраты на использование, приходящиеся на НИОКР
Компьютер | 100000 | 1 | 62 | 4,00% | 2192
Ноутбук | 110000 | 3 | 219 | 4,00% | 7233
Принтер со сканером | 25000 | 1 | 150 | 2,00% | 205
Осциллограф | 25000 | 1 | 100 | 1,16% | 159
Паяльная станция | 10000 | 1 | 100 | 0,56% | 15
Итого | | | | | 9 804,38 ₽

Транспортно-заготовительные расходы, составляющие 5 % от величины основных затрат на материальные ресурсы:

34360 руб. ∙ 5 % = 1718,00 руб.

## 3.4. Затраты на специальное программное обеспечение

Провeдeниe НИОКР требует использования специального ПО.

- Компас 3D, Inventor CAM – для проектирования эскизного проекта, оформления рабочей документации;
- Altium Designer – для проектирования электронных схем;
- Coube MX и CubeIDE – для настройки микроконтроллера;
- MATLAB - для математического моделирования;
- Операционная система - Windows;
- Пакет офисных программ.

Затраты на программное обеспечение включают покупку лицензий на программные продукты, использующиеся в НИОКР, а также отчисления на использование собственных программных продуктов. Расчет затрат на программное обеспечение производится в соответствии с формулами амортизационных отчислений.

Программы приобретаются единым платежом и не содержат подписочных сервисов. Срок использования программ приравняем сроку службы компьютеров. Тогда амортизация:

Результаты оценки затрат на программное обеспечение

Таблица 4. Расчёт затрат на ПО

Наименование | Стоимость лицензии, руб. | Количество устройств | kа, % | Величина затрат, руб.
Операционная система | 12000 | 4 | 4,00% | 1 052
Пакет офисных программ | 10000 | 4 | 4,00% | 877
MATLAB | 50000 | 1 | 4,00% | 1 096
Altium Designer | 110000 | 1 | 4,00% | 2 411
Компас 3D | 150000 | 1 | 4,00% | 3 288
Итого | | | | 8 723,29 ₽

## 3.5. Общая величина затрат

Величина общих затрат представлена в таблице 5:

Таблица 5. Итоговые затраты

Тип затрат | | Величина затрат, руб.
Затраты на материальные ресурсы | 34 360 | 34 360
| 9 804 | 9 804
Транспортно-заготовительные затраты | | 1 718
Затраты на программное обеспечение | | 8 723
Затраты на оплату труда работников | | 3 547 799
Накладные расходы | | 5 321 698,5
Итого | | 8 924 102,5 ₽

# 4. Оценка эффективности проведения НИОКР

Формирование цен на научно-техническую продукцию осуществляется, как правило, на договорно-контрактной основе, цена (Цнп) устанавливается по соглашению сторон. При этом предприятие-исполнитель и предприятие-потребитель, заключая договор-контракт, принимают на себя определенные обязательства.

Примем цену за научно-техническую продукцию в 2 раза больше себестоимости: Цнп=17 848 205

В ОЭЧ валовая прибыль как финансовый результат НИОКР рассчитывается как разность:

Пв = (Цнп + РИНИОКР) – Снп,

Где:

РИНИОКР – реализация имущества, использованного при выполнении данных НИОКР;

П_в – валовая прибыль;

С_(нп) – себестоимость конечной продукции.

С учетом того, что все оборудование имеется в наличии на предприятии и оно используется в ряде других проектов, то после проведения этого НИОКР оборудование не реализуется, следовательно, примем РИНИОКР = 0.

Тогда П_в =17 848 205- 8 924 102,5 =8 924 102,5 ₽.

Чистая прибыль Пч – это часть валовой прибыли, остающейся в распоряжении предприятия после уплаты налогов и других обязательных платежей в бюджет.

В ОЭЧ чистая прибыль условно определяется с учетом налога на прибыль (Нп):

П_ч =П_в -Н_П

Примем Н_п =П_в *20%=1 784 820,5 .

П_ч =8 924 102,5-1 784 820,5=7 139 282 ₽.

Рентабельность затрат на НИОКР определяется по формуле:

Р_(НИОКР) =(П_ч)/(С_(нп))=(7 139 282)/(8 924 102,5)=0.8=80%

По данному показателю видно, что продукция окупаема. Этот показатель рекомендуется не опускать ниже 20%.

Научно-техническую ценность результатов НИР (ЦНТНИР) можно вычислить следующим образом:

ЦНТНИР=р·Мi·bi

n – число признаков, участвующих в оценке;

Мi – оценка результата НИР по –тому признаку в баллах;

bi – коэффициент значимости –того признака;

р – вероятность получения ожидаемого результата

Показатели признаков, их характеристика и оценка в баллах приведены в таблице 6.

Признак (весомость признака bi) | Показатели признака | Характеристика | Оценка Мi, баллы
Новизна результатов НИР (0,34) | Превышает мировые достижения | Получение принципиально новых результатов, неизвестных науке, разработка оригинальных теорий, принципиально новых устройств, веществ, способов | 9-10
| Находится на уровне мировых достижений | Установление некоторых общих закономерностей, разработка новых устройств, методов, способов, алгоритмов, принципиальные усовершенствования | 7-8
| Приближается к мировым достижениям | Положительное решение поставленных задач на основе простых обобщений, анализ связей между фактами, распространение известных принципов на новые объекты, воспроизводство устройств, агрегатов. | 3-5
| Тривиальный | Описание отдельных элементарных факторов, реферативные обзоры, передача и распространение опыта | 1-2
Широта использования результатов НИР (0,33) | Значительная | Могут найти применение в изделиях нескольких отраслей | 8-10
| Средняя | Могут найти применение в изделиях одной отрасли | 4-7
| Слабая | Могут найти применение в изделиях одного типа | 1-3
Степень воздействия результатов на качество объекта НИР (0,33) | Значительная | Позволяют существенно улучшить основной признак, характеристику, процесс | 9-10
| Средняя | Улучшают основные параметры изделия или процесса | 6-8
| Слабая | Позволяют существенно улучшить второстепенные, вспомогательные устройства или параметры | 3-5
| Незначительная | Способствуют незначительному улучшению второстепенных параметров и устройств | 1-2

Таблица 6. Признаки для оценки научно-технической ценности НИР

ЦНТ_(НИР) = р*∑Mi*bi=0.85*(0.34*5+0.33*10+0.33*8) = 6.5

# 5. Заключение

По итогу проделанной работы были определены этапы проведения НИОКР по разработке привода направленной антенны, произведён расчёт затрат на выполнение НИОКР и сделаны выводы о целесообразности её проведения.

Названия этапов и их длительность представлены в виде ленточного графика, иллюстрирующего особенности НИОКР. Чистая прибыль составит 7 139 282 руб, рентабельность проекта составляет 80%, показатель научно-технических результатов равен 6,5, что является хорошим результатом.

В результате создаваемое изделие соответствует как экономическим, так и техническим нормам, что позволяет провести его разработку и осуществлять дальнейшее производство для предполагаемых отраслей.

Результаты данного НИОКР можно использовать для наладки серийного производства изделия. Затраты на компоненты изделия составляют менее 35 000 руб. для опытного образца.

Исходя из этого сделан вывод о целесообразности проведения НИОКР по данному проекту.

# 6. Список литературы

1. Организация и планирование машиностроительного производства (производственный менеджмент): Учебник/ К.А. Грачева, М.К. Захарова, Л.А. Одинцова и др.; под ред. Ю.В. Скворцова, Л.А. Некрасова. – М.: Высш. Шк., 2003. – 470 с.
2. Налоговый кодекс Российской Федерации (часть вторая) от 05.08.2000 N 117-ФЗ (ред. от 27.11.2018) // Собрание законодательства РФ, N 31, 03.08.1998, ст. 3824.
3. Иванова Н.Ю., Савченко Н.Н. Организация и планирование проведения НИОКР – М.: Изд-во МГТУ им. Н.Э. Баумана, 2008. - 18 с.
4. Савченко Н.Н. Технико-экономический анализ проектных решений. - М.: Изд-во «Экзамен», 2002. - 128 с.
5. Сайт судебных и нормативных актов РФ [электронный ресурс] URL: https://sudact.ru/law/prikaz-minstroia-rossii-ot-08022017-n-77pr/metodika-primeneniia-smetnykh-tsen-stroitelnykh/4/tablitsa-1/
6. Сайт поставщика среды Matlab Simulink [электронный ресурс]. URL: https://www.mathworks.com
7. Сайт поставщика проектирования печатных плат Altium Designer [электронный ресурс]. URL: https://www.altium.com

# Приложение А

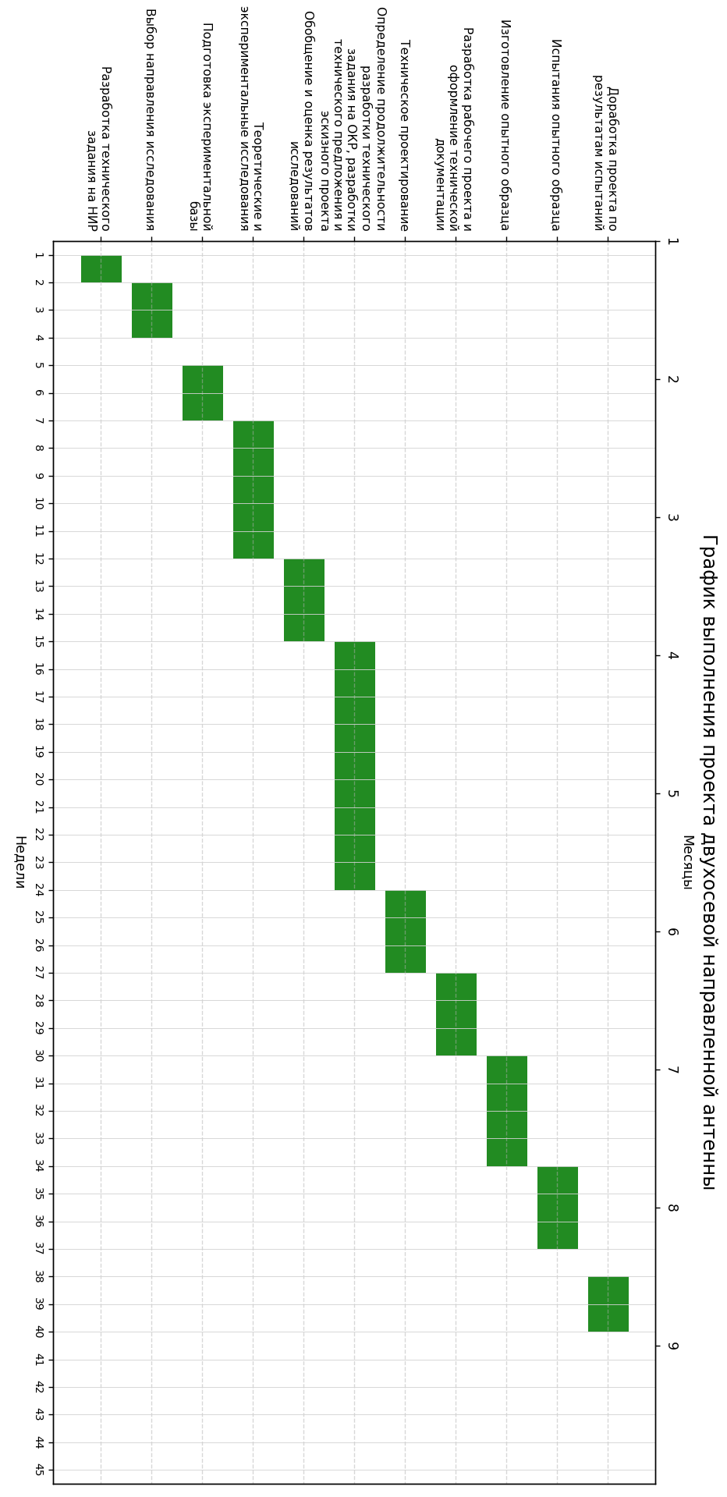
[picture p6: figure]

# Приложение Б

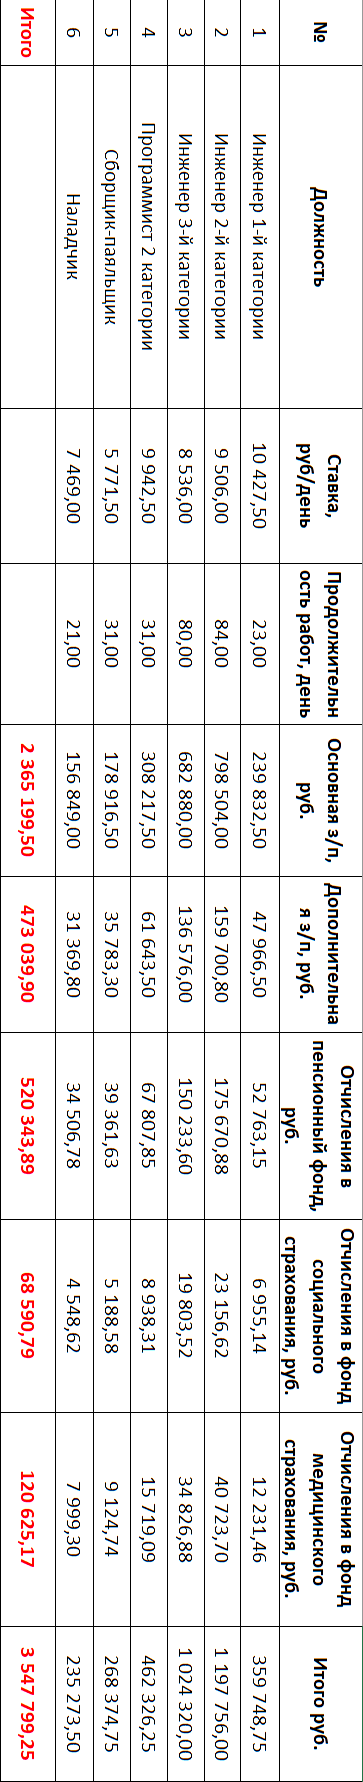
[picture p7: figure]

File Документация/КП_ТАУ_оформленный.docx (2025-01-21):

| Министерство науки и высшего образования Российской Федерации Федеральное государственное бюджетное образовательное учреждение высшего образования «Московский государственный технический университет имени Н.Э. Баумана (национальный исследовательский университет)» (МГТУ им. Н.Э. Баумана)

ФАКУЛЬТЕТ «Специальное машиностроение»

КАФЕДРА «Робототехнические системы и мехатроника»

РАСЧЕТНО-ПОЯСНИТЕЛЬНАЯ ЗАПИСКА

К КУРСОВОЙ РАБОТЕ

НА ТЕМУ:

Разработка двухосевого привода направленной антенны для установки на БПЛА

Студент СМ7-72Б _________________ Санников А.К.

(Группа) (Подпись, дата) (И.О.Фамилия)

Руководитель _________________ Гуляев И.А.

(Подпись, дата) (И.О.Фамилия)

Консультант _________________ ____________________

(Подпись, дата) (И.О.Фамилия)

2024 г.

Министерство науки и высшего образования Российской Федерации

Федеральное государственное бюджетное образовательное учреждение

высшего образования

«Московский государственный технический университет имени Н.Э. Баумана

(национальный исследовательский университет)»

(МГТУ им. Н.Э. Баумана)

УТВЕРЖДАЮ

Заведующий кафедрой __________

(Индекс)

______________ _______________

(И.О.Фамилия)

« _____ » ____________ 20 ____ г.

ЗАДАНИЕ

на выполнение курсовой работы

По теме: | Разработка двухосевого привода направленной антенны

для установки на БПЛА

Студент группы ____СМ7-72б___________

_________________________Санников Артём Константинович__________________________

(Фамилия, имя, отчество)

Направленность КР (учебная, исследовательская, практическая, производственная, др.)

________практическая____________________________________________________________

Источник тематики (кафедра, предприятие, НИР) ____НИР______________________________

График выполнения КР: 25% к 5 нед., 50% к 7 нед., 75% к 10 нед., 100% к 14 нед.

Техническое задание | Разработать САУ двухосевого привода для встраивания в систему

ретрансляции сигнала с возможностью установки на БПЛА для увеличения дальности

передачи сигнала

Оформление курсовой работы:

Расчетно-пояснительная записка на _____ листах формата А4.

Перечень графического (иллюстративного) материала (чертежи, плакаты, слайды и т.п.)

_______________________________________________________________________________

_______________________________________________________________________________

_______________________________________________________________________________

Дата выдачи задания « 17 » сентября 2024 г.

Руководитель НИР _________________ Гуляев И.А.

(Подпись, дата) (И.О.Фамилия)

Студент _________________ Санников А.К.

(Подпись, дата) (И.О.Фамилия)

Примечание: Задание оформляется в двух экземплярах: один выдается студенту, второй хранится на кафедре.

СОДЕРЖАНИЕ

# ТЕХНИЧЕСКОЕ ЗАДАНИЕ

На этапе научно-исследовательской работы была разработана кинематическая схема двухосевого привода направленной антенны, а также сформулированы технические требования к САУ. В связи с этим, сформулируем цель курсовой работы.

Цель работы— разработать математическую модель двухосевого привода, построенного на основе синтезированной кинематической схемы (рис. 1). По построенной модели создать систему автоматического управления приводом.

Для достижения приведенной цели необходимо решить следующие задачи:

- На основании поставленного технического задания и научно-исследовательской работы составить информационную модель привода с помощью MATLAB и Simulink, составить структурную схему.
- С помощью разработанной модели провести энергетический расчет привода, получить модель неизменяемой части системы автоматического управления (САУ).
- Провести анализ качества работы нескорректированной системы.
- Выбрать архитектуру корректирующего устройства, получить его математическую модель.
- Получить разностное уравнение для реализации корректирующего устройства в микроконтроллере
- Сформулировать выводы по проделанной работе и дать оценку спроектированной системы.

Конкретные числовые значения величин представлены в таблице ТЗ 1.

Таблица 1. Техническое задание на разработку привода

Параметр | Значение | Ед. измерения
Общая масса | 2700 | г.
Предельные габариты | 300х300х300 | мм
Напряжение питания | 12 | В
Диапазон вращения оси 1 | 0≤φ≤360 | °
Диапазон вращения оси 2 | -180≤γ≤0 | °
Угловая скорость вращения осей | 87,26 | рад/с
Угловое ускорение вращения осей | 872,66 | рад/с ²
Время переброски на 360° (время переходного процесса) | 0.125 | сек
Ошибка слежения | 1 | °
Перерегулирование при переброске | 25 | %

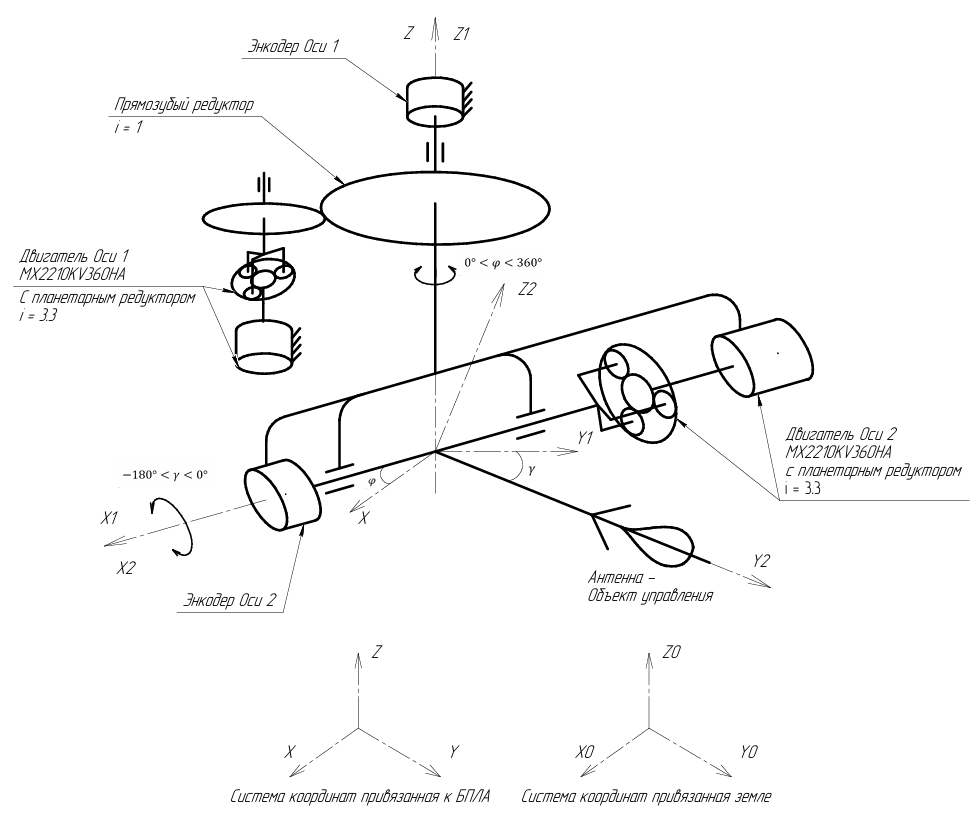
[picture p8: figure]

Рис. 1 Кинематическая схема привода

# 1 Энергетический расчет привода

В ходе научно-исследовательской работы было определены требуемые характеристики привода путем построения 3-д модели (рис. 2), получившиеся параметры, также-стоит сразу отметить, что для обоих осей привода было принято решение использовать одинаковые двигатели в соответствии с этим энергетический расчет будет проводится 1 раз для более нагруженной 1 оси, полученные данные после 3-д моделирования:

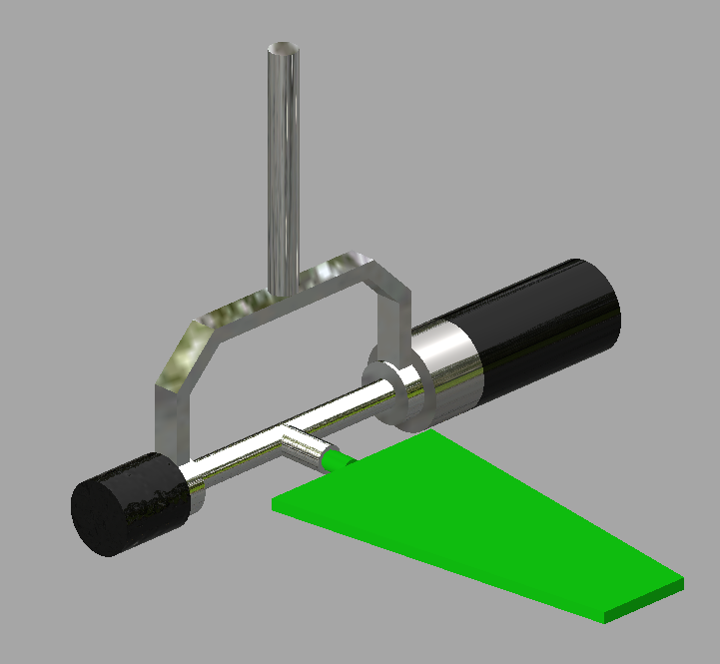
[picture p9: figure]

Рис. 2 Грубая 3Д модель привода для оценки моментов инерции.

Рассчитанный момент инерции конструкции:

| I_(yy) = 748,534 кг мм^2 =7.48534*10^(-5) кг м^2 | (1)

Тогда требуемый максимальный момент на выходном валу:

| M_m =I_(yy) *ε=872,66*7.48534*10^(-5) =0.0653 Н*м | (2)

Расчет эквивалентной скорости:

| Ω_(экв) = τ_(ΩД) ∙ε+ω= 0,05∙872,66 +87,26=130,89 рад/с | (3)

τ_(ΩД) - постоянная времени разгона, для приводов с транз. УМ. Примем τ_(ΩД) = 0,05 с

Расчет граничного значения макс. требуемой мощности привода:

| P_М = (Ω_(экв) ∙M_m)/(η_(пх))=(130,89∙0.0653)/(0,8)=10,68 Вт | (4)

Расчет ориентировочного значения требуемой номинальной мощности двигателя:

Примем, что макс. мощность привода равна макс. требуемой мощности P_(max) =P_м .

Для двигателя с жесткой механической характеристикой λ_(КД) ≥ 8..10:

Требуемая мощность двигателя: P_(ДН1) =(P_(max))/(2..3,5)

Для двигателя с недостаточной жесткой механикой λ_(КД) = 2..5:

Требуемая мощность двигателя: P_(ДН2) =(P_(max))/(1..1,56)

Получаем:

| P_(ДН1) =(P_(max))/(2,5)=(10,68)/(2,5)=4,272 Вт | (5)
| P_(ДН2) =(P_(max))/(1,5)=(10,68)/(1,5)=7,12 Вт | (6)

Также в ходе научно-исследовательской работы был выбран BLDC двигатель MX2210KV360HA с планетарным редуктором и передаточным отношением 3.3. Помимо мощности на выбор повлияло наличие планетарного редуктора и характеристики максимального момента.

Параметры двигателя приведены в таблице 1:

Таблица 2. Характеристики двигателя и редуктора

Характеристика | Значение | Ед. измерения
Мощность | 15 | Вт
Номинальные обороты | 3300 | Об/мин
Номинальный момент | 0.033 | Н*м
Момент страгивания | 0.105 | Н*м
Момент инерции ротора | 0.00000076 | Кг м²
Индуктивность обмотки | 100 | мкГн
Сопротивление обмотки | 750 | мОм
Номинальное напряжение | 12 | В
Передаточное отношение редуктора | 3.3 | -
Количество полюсов | 7 | -
KV | 360 | -
Постоянная момента K_М | 0.023 | Н*м/А
Постоянная противо-ЭДС K_Ω | 0.023

Номинальная угловая скорость двигателя:

| Ω_(ДН) =(π∙N_Н)/30=(π*3300)/30=345,57 рад/с | (7)

Номинальный момент двигателя:

| М_(ДН) =(P_(ДН))/(Ω_(ДН))=15/(345,57)=0,043 Н∙м | (8)

Также необходимо пересчитать индуктивность и сопротивление обмоток, так как производитель указывает сопротивление и индуктивность одной обмотки и указывает схему подключение - звезда:

| R_Я =R_(1ph) +1/(1/(R_(1ph))+1/(R_(1ph)))=1.125 Ом | | (9)
| L_Я =L_(1ph) +1/(1/(L_(1ph))+1/(L_(1ph)))=0.00015 Гн | (10)

Выбор усилителя мощности:

- Определяем сопротивление цепи:

| R_Д =R_(УМ) +R_Я | (11)

Для транзисторного УМ R_(УМ) =0 , тогда R_Д =R_Я =1,125 Ом - назначим коэффициент форсирования двигателя по напряжению λ_(СК.М) = 1 для транзисторных УМ => U_(max) =U_(ЯН)

- определяем допустимое упр. напряжение (λ_(СК) =0,8..0,9):

| U_(ЯД) =λ_(СК) ∙U_(ЯН) =0,9∙12=10,8 В | (12)

- определяем доп. значение момента (λ_М =1,5..2):

| М_(ДД) =λ_М ∙М_(ДН) =2∙0,043 =0,086 Н∙м | (13)

- определяем доп. макс. значение момента (λ_(ММ) =4):

| М_(ДМ) =λ_(ММ) ∙М_(ДН) =4∙0,043=0,172 Н∙м | (14)

Расчет передаточного отношения:

а) Проверка условия по моменту:

| М_(ДТ) (i)=(M_m)/(i∙η_(пх))+J_Д ∙i∙ε≤М_(ДД) =λ_М ∙М_(ДН) 0.0653/(i∙0,8)+0,76∙ 10^(-6) ∙i∙872,66=0,086 | (15)

Решаем квадратное уравнение и получим диапазон i:

i_1 ≈1 округлили в большую сторону

i_2 ≈128 округлили в меньшую сторону

б) Проверка условия по напряжению:

| U_(ЯМ) (i)=(R_Я)/(K_М)∙((M_m)/(i∙η_(пх))+J_Д ∙i∙ε)+K_Ω ∙i∙ω≤U_(ЯД) (1,125)/(0,023)(0.0653/(x∙0,8)+0,76∙ 10^(-6) ∙x∙872,66)+0,023∙x∙87.26=10,8 | (16)

Решаем квадратное уравнение и получим диапазон i:

i_1 ≈1 округлили в большую сторону

i_2 ≈4 округлили в меньшую сторону

Скорость холостого хода:

| Ω_(ДХ) =(U_(ЯД))/(K_Ω)=(10,8)/(0,023)=469,56 рад/с | (17)

Постоянная времени для выбранного двигателя:

| τ_(ΩД) ^(*) =(R_Я ∙J_Д)/(K_М ∙K_Ω)=(1,125∙0,76∙ 10^(-6))/(0,023∙0,023)=0,0016 с | (18)

Эквивалентная скорость:

| Ω_Э = τ_(ΩД) ^(*) ∙ε+ω= 0,0016∙872,66+87.26=88,65 рад/с | (19)

Граничное значение максимально требуемой мощности:

| P_М = (Ω_Э ∙M_m)/(η_(пх))=(88,65∙0.0653)/(0,8)=7,23 Вт | (20)

Пусковой момент (согласно документации):

| М_П =0,105 Н∙м | (21)

Максимальная мощность:

P_(max) =0,25∙М_П ∙Ω_(ДХ) =0,25∙0,105∙469,56 =12,32 Вт | (22)

P_(max) ≥P_М – условие выполняется.

Определяем общий диапазон передаточных отношений из условий а) и б):

Общий диапазон передаточных отношений: 1 ... 4

Выбираем передаточное отношение 3.3 так как производитель предлагает готовый планетарный редуктор с таким передаточным отношением (рис. 3)

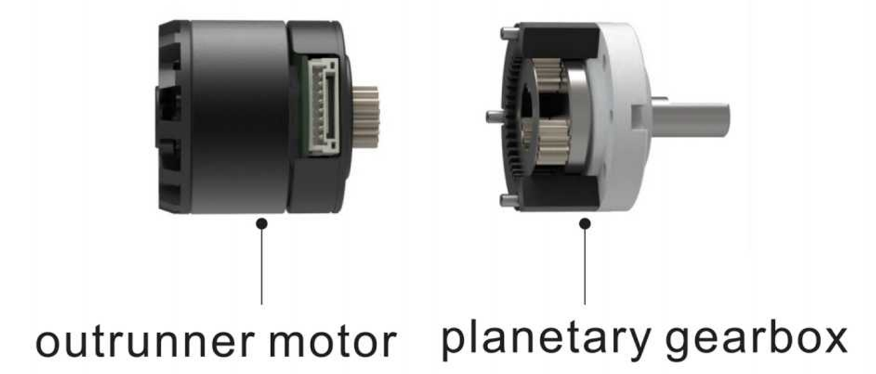
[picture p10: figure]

Рис. 3 Планетарный редуктор к выбранному двигателю

Проверочный расчет:

Определяем требуемый момент на валу двигателя:

| M_m^(*) =(M_m)/(i∙η_(пх))=0.0653/(3.3∙0,8)=0,024 Н∙м М_(ТД) = M_m^(*) +J_Д ∙i∙ε=0,024+0,76∙10^(-6) ∙3.3∙872,66= 0,026 Н∙м 0,086 Н∙м=М_(ДД) ≥М_(ТД) – условие выполняется. | (23)

Определяем требуемую скорость вращения вала двигателя:

| Ω_(ТД) =i∙ω=3.3∙87,26=287.95(рад)/с 345,57 рад/с=Ω_(ДН) ≥Ω_(ТД) - условие выполняется. | (24)

Определяем требуемое напряжение в цепи:

| U_(ЯТ) =(R_Я)/(K_М)∙М_(ТД) +K_Ω ∙Ω_(ТД) =(1,125)/(0,023)∙0,026 + 0,023∙287,95=7,89 В U_(ЯД) <U_(ЯТ) - условие выполняется | (25)

Таким образом – двигатель выбран верно так как все условия выполняются. Для обоих осей, в целяхупрощения выбираем эту пару двигателя и редуктора, так как на вторую ось такие же требования, за исключением меньшего момента и момента инерции.

# 2 Моделирование неизменяемой части привода

Для начала создадим модель двигателя в среде Simulink. Модель представлена на рисунке 4. Двигатель является трехфазным бесколлекторным, однако в процессе моделирования использовалась эквивалентная модель по аналогии с ДПТ.

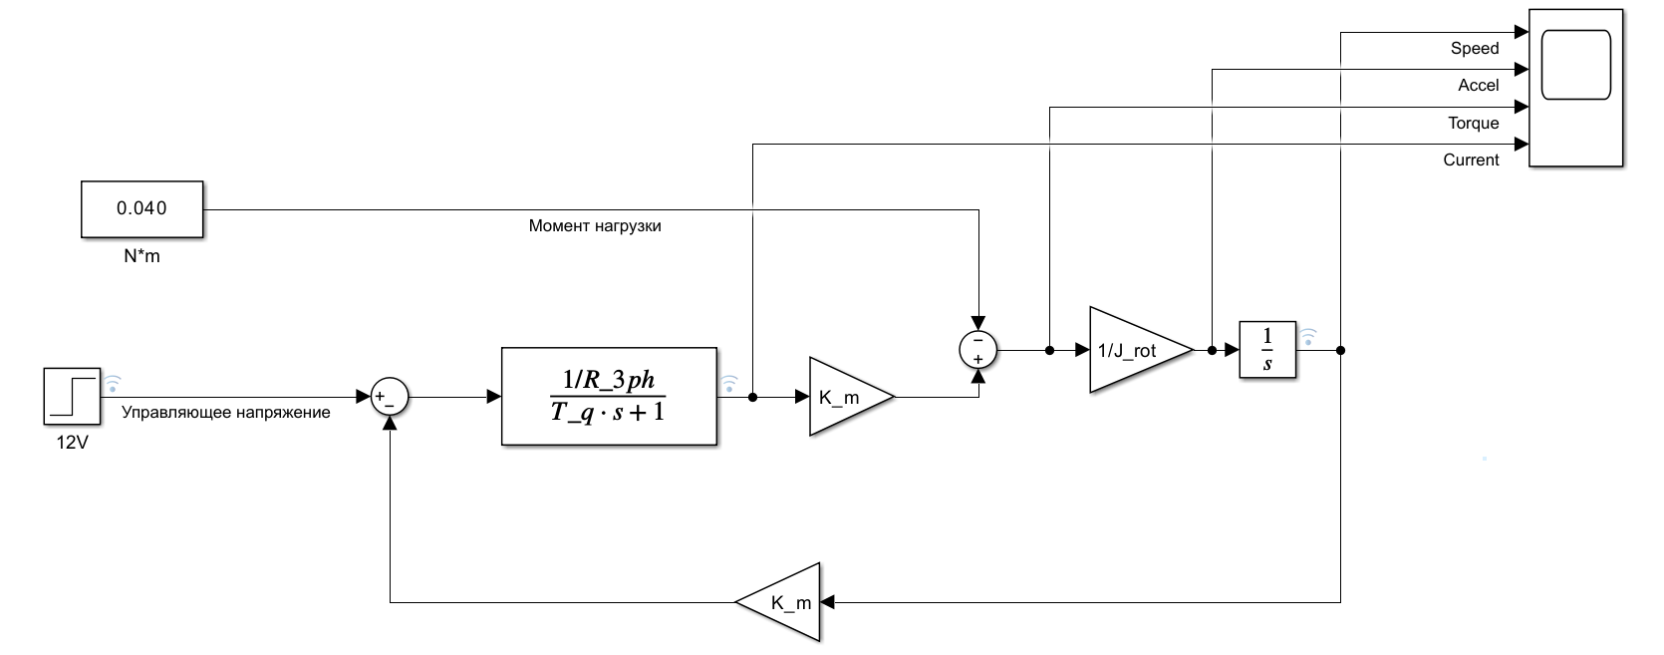
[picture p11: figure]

Рис. 4 Модель двигателя MX2210KV360HA

Листинг 1. Код matlab с параметрами двигателя

% Двигатель MX2210KV360HA

L_1ph = 0.0001; %Гн

R_1ph = 0.75; %Ом

W = 450; %рад/c без нагрузки

U_dvig = 12; %В

I_noload = 0.15; %А

J_rot = 0.00000075;

P_amt = 7;

nu = 0.84; %КПД

K_m = 0.023; %Н*м/А

L_3ph = L_1ph + 1/(1/L_1ph + 1/L_1ph)

R_3ph = R_1ph + 1/(1/R_1ph + 1/R_1ph)

K_w = 0.023;

K_omega = 0.023;

T_q = L_3ph/R_3ph;

T_m = 0.000098;

Добавляем в систему редуктор и собираем общую линейную модель неизменяемой части без коррекции, представлена на рис. 5:

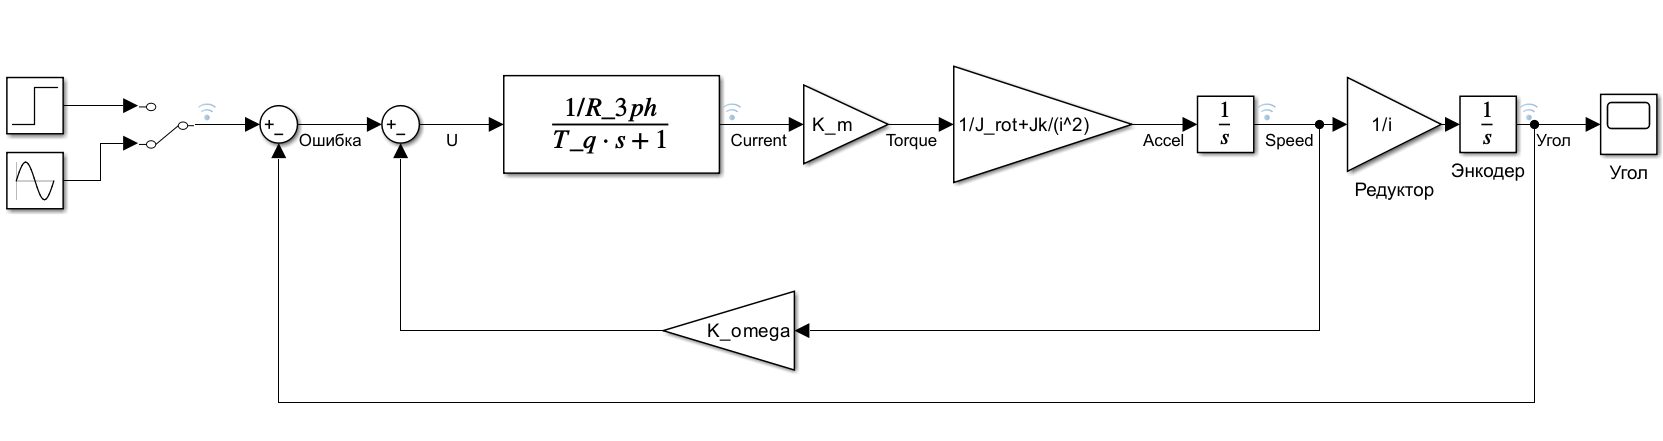
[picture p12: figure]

Рис. 5 Модель привода в Simulink

Определяем передаточную функцию неизменяемой части:

Параметры привода:

| K_М =0.023 Н∙м / А; K_ω =0.023 (В∙с)/(рад); J_Σ =J_(дв) +(J_(К MAX))/(i^2)=0.76∙ 10^(-6) кг∙м^2 +(7.48534*10^(-5) кг∙м^2)/(3.3^2)≅7,633∙10^(-6) кг∙м^2 | (26)

Рассмотрим электрическую и электромеханическую постоянные времени:

| T_(ЭМдв) =(J_(дв) R_Я)/(K_М K_ω)=(0,76∙10^(-6) ∙1,125)/(0,023 ∙0,023)=0,0016 c T_Э ≈ 0,1 T_(ЭМ) для двигателей мощностью до 100 Вт: T_(Эдв) =0,1T_(ЭМ) =0,00016c L_Я =0,00015 Гн T_(ЭМпр) =(J_Σ R_Я)/(K_М K_ω)=(7,633∙10^(-6) ∙1,125)/(0,023 ∙0,023)=0,0162 c для привода с учетом нагрузки | (27)

Передаточная функция неизменяемой части привода будет иметь вид:

| | W_(нч) (s)=(1/(K_ω *i))/(s(T_(ЭМпр) *T_(Эдв) *s^2 +T_(ЭМпр) *s+1))==(1/(0,023*3,3))/(s(0,0162*0,00016*s^2 +0,0162*s+1)) W_(нч) (s)= 13.1752/(s(0.01603s+1)(0.0001616s+1)) | (28)

ω_1 =1/0.01603=62.35 с^(-1) ; ω_2 =1/0.0001616=6187.65 с^(-1)

## 2.1 Анализ нескорректированной системы

Проведем анализ работы системы без ввода корректирующих устройств, рассмотрим работу системы в режиме слежения:

| g(t)=Asin(ω_р t) g(t)=Aω_р cos(ω_р t) g(t)=-Aω_p^2 sin(ω_р t) max(g(t))=Aω_р =87,26 ((рад)/с) max(g(t))=Aω_p^2 =872,66 ((рад)/(с^2)) | (29)

Из системы двух уравнений получим рабочую частоту и амплитуду:

| A=8.72 (рад) ω_р =10 (1/с) | (30)

Допустимая ошибка по тз:

| ε=1°=0,017453 (рад) | (31)

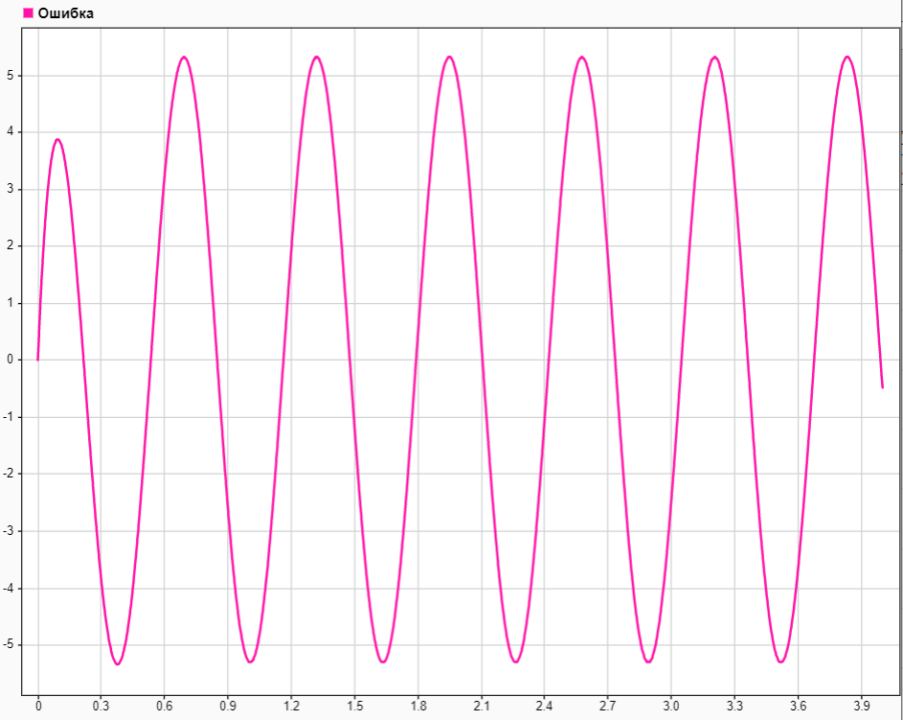
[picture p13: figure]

Реакция системы на режим слежения представлена на рис. 6. Как видно из графика, динамическая ошибка составляет порядка 5 рад, что значительно превышает заданную ошибку.

Рис. 6 Реакция нескорректированной системы на режим слежения

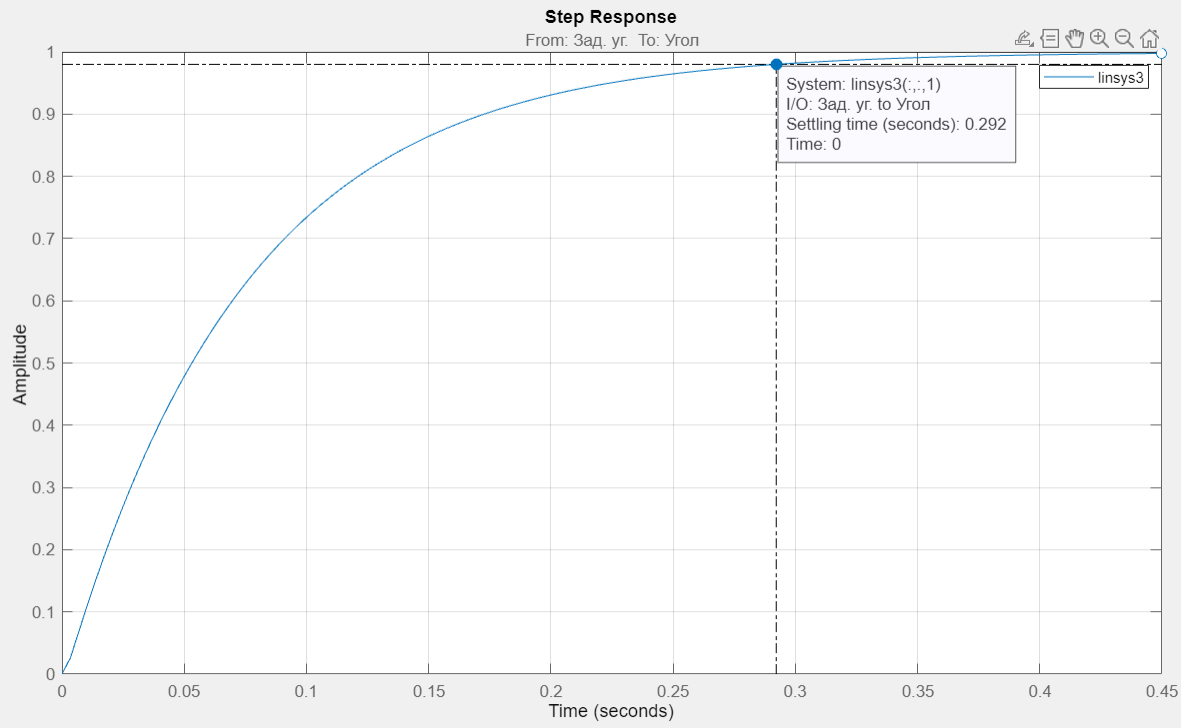
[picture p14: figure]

Рассмотрим реакцию системы на режим переброски (рис.7) , исходя из ТЗ переброска на 1 радиан должна занимать 0.02 сек :

Рис. 7 Реакция на режим переброски

ЛАЧХ и ЛФЧХ системы представлены на рис. 8. Исходя из них можно сделать вывод об устойчивости исходной системы.

Рис. 8 ЛАЧХ и ЛФЧХ нескорректированной системы

По итогу проведенного анализа можно судить что система не удовлетворяет требованиям ТЗ и нуждается к корректировке.

# 3 Построение желаемой ЛАЧХ и синтез корректирующего устройства

Для обеспечения технических требований вводим корректирующие устройства, для начала попробуем внедрить последовательное корректирующее устройство. Воспользуемся частотным методом синтеза и построим желаемую ЛАЧХ и ЛАЧХ неизменяемой части. Поскольку система продолжительное время работает в режиме слежения, будем строить ЛАЧХ в режиме слежения.

| | W_(нч) (s)= 13.1752/(s(0.01603s+1)(0.0001616s+1)) | (32)

ω_1 =1/0.01603=62.35 с^(-1) ; ω_2 =1/0.0001616=6187.65 с^(-1)

20lg(k)=20lg(13.1752)= 22.39 дБ

Для желаемой ЛАЧХ определим рабочую точку и частоту среза исходя из ТЗ:

| Wж( ω_р )=20lg⁡(A/ε ) + 3 = 20lg⁡(8.72/(0,017453) ) + 3 = 56.97 Дб ω_р =10 (1/с) | (33)

Расчет частоты среза:

Расчет будем производить из условий, накладываемых на время переходного процесса t_(пп) ≤0,02с и перерегулирование σ≤10% .

Выберем перерегулирование σ=20% , тогда по диаграмме Солодовникова t_(пп) =(2.7π)/(w_с) . Из условия для времени переходного процесса определяем частоту среза

w_(ср) =424.15 c^(-1) , которой соответствует t_(пп) =0,02с .

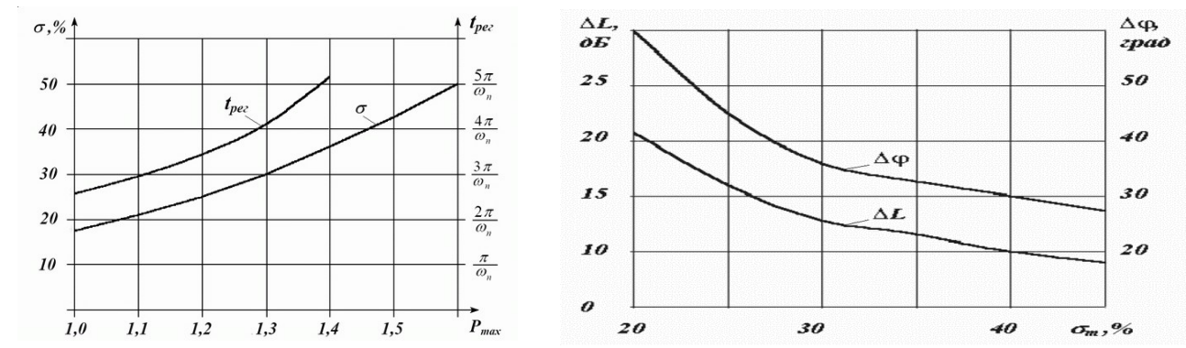
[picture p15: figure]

Рис. 9 Диаграммы Солодовникова

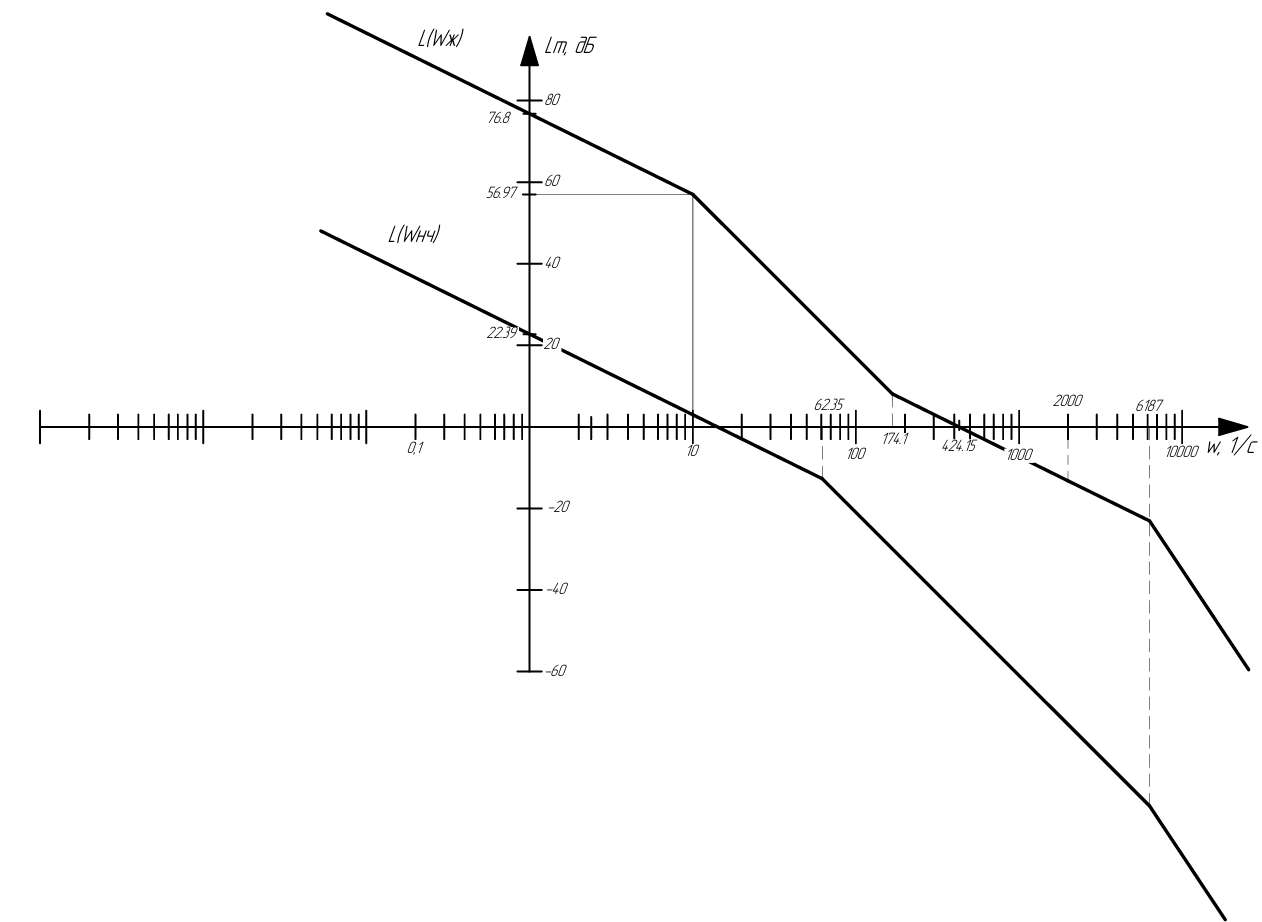
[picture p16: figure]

Построения желаемой ЛАЧХ и ЛАЧХ и неизменяемой части представлено на рисунке 10:

Рис. 10 ЛАЧХ желаемая и неизменяемая часть

Определим передаточную функцию желаемой системы:

| 20lgk = 76.8 => k = 6918.3 T_1 =1/(ω_р)=0.1 T_2 =1/174.1=0.0057 T_3 =1/6187.65=0.0001616 T_4 =1/(ω_2)=1/6187.65=0.0001616 W_ж =(6918.3(0,0057s+1))/(s(0,1s+1)(0,0005s+1)(0,0001616s+1)) | (34)

Тогда передаточная функция корректирующего устройства:

| W_п =(W_ж)/(W_(нч))==(6918.3(0,0057s+1)s(0.01603s+1)(0.0001616s+1))/(13.1752*s(0,1s+1)(0,0001616s+1)(0,0001616s+1))=(525.1(0,0057s+1)(0.01603s+1))/((0,1s+1)(0,0001616s+1)) | (35)

Построим модель корректирующего устройства(рис. 11):

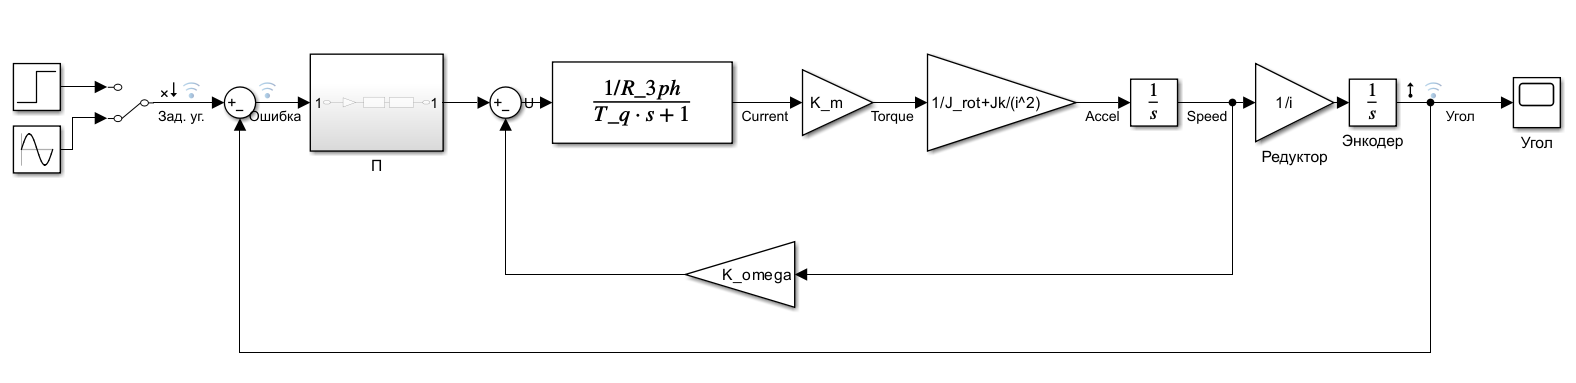
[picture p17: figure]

Рис. 11 Последовательное корректирующее устройство

Рис. 12 Система с коррекцией

Проведем анализ полученной модели на удовлетворение техническим требованиям, для начала параметры переходного процесса:

Рис.13 Переходной процесс после коррекции

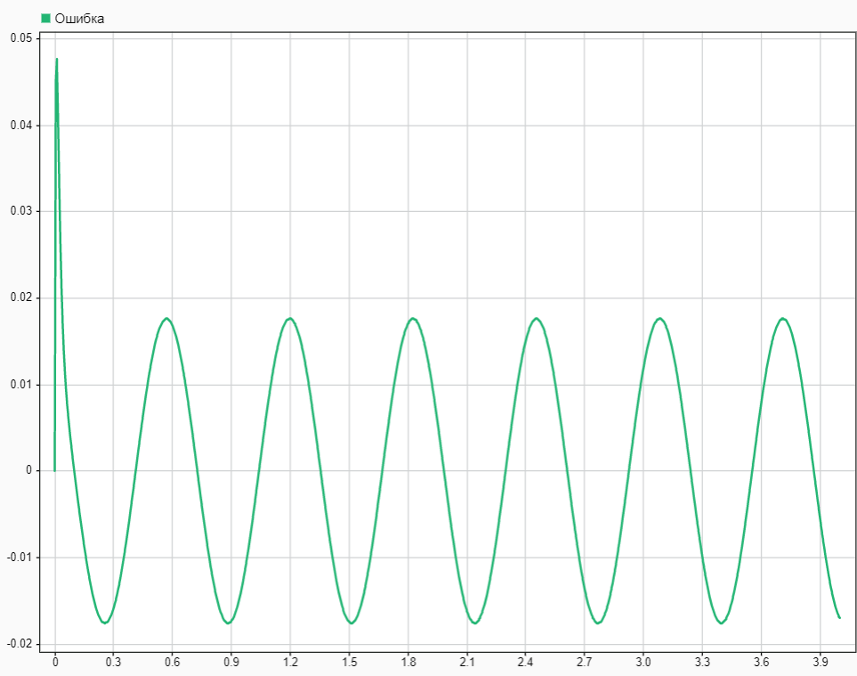
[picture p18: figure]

Как видно из графика техническое задание по режиму переброски выполнено успешно. Далее посмотрим режим слежения, графики ошибки представлены на рис. 14.

Рис. 14 Динамическая ошибка после коррекции

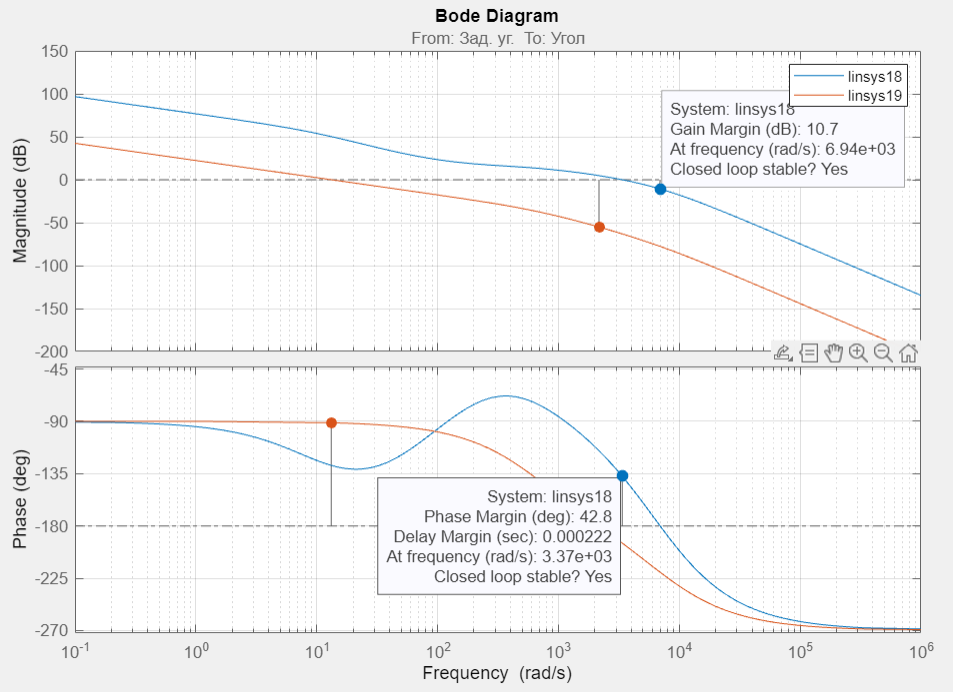
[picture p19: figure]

Рис. 15 ЛАЧХ и ЛФЧХ получившейся системы

На рис. 15 можно наблюдать сравнение ЛАЧХ и ЛФЧХ системы до и после коррекции.

# 4 Уточнение модели при помощи нелинейностей

Далее стоит применить к модели некоторые уточнения путем введения нелинейности, здесь стоит отметить мертвую зону, которая отражает напряжение трогания двигателя, и блоки ограничения. Блок ограничения по напряжению недопускает повышение напряжения на двигателе выше, чем 90% от номинального напряжения. Блок ограничения по току не дает тому расти выше 3А что является рекомендацией производителя двигателя. На рис. 16 приведена уточненная модель.

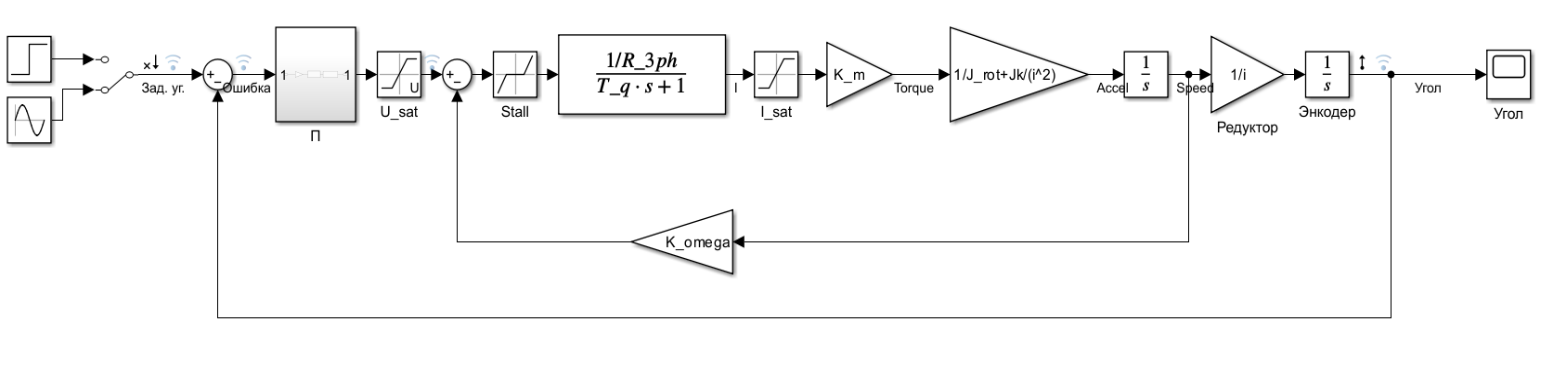
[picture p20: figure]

Рис. 16 Модель с нелинейными элементами

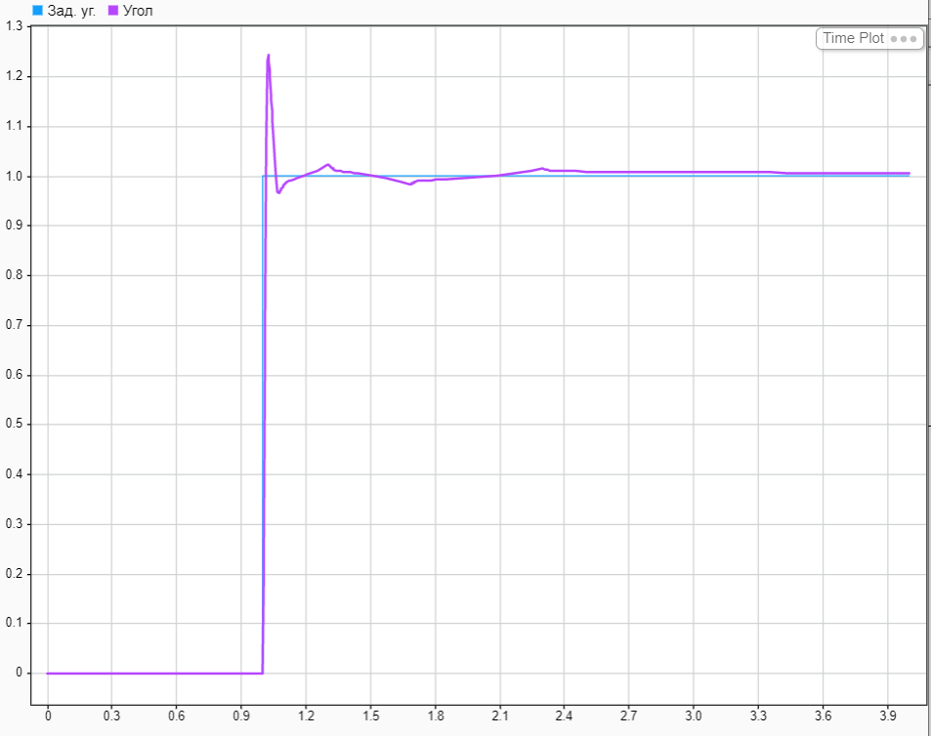
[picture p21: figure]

Проведем анализ уточненной модели, посмотрим на переходной процесс, изображенный на рисунке 17.

Рис. 17. Переходной процесс с учетом нелинейности

Заметим что время переходного процесса незначительно увеличилось как и перерегулирование, однако такие показатели также вписываются в техническое задание. Теперь посмотрим на динамическую ошибку. Графики динамической ошибки и напряжения в режиме слежения представлены на рис. 18.

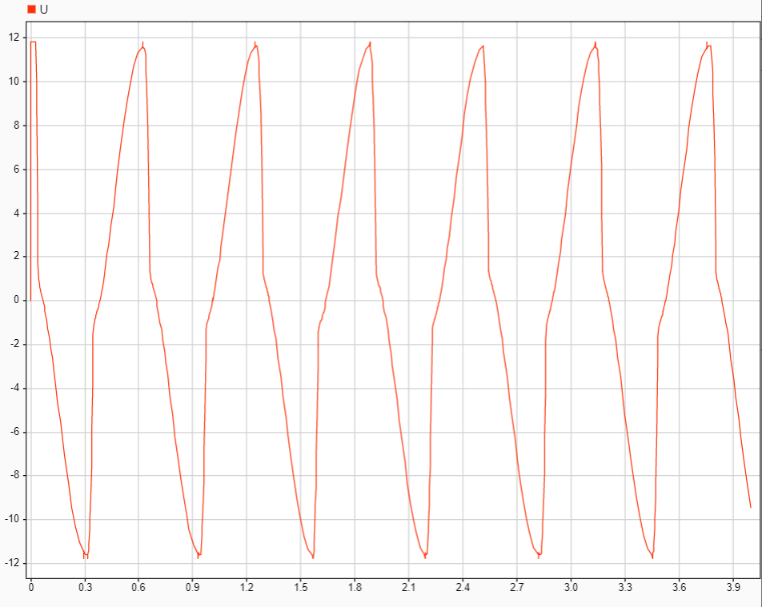
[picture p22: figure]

Рис. 18 Управляющее напряжение и ошибка

Заметим, что управляющее напряжение теперь в норме, и удалось избавиться от скачков, динамическая ошибка при этом обрела кратковременные скачки, которые выбиваются за пределы заданые в ТЗ, однако влияние таких скачков несущественно в рамках общей картины.

# 5 Анализ дискретной системы

На данном этапе разработки период дискретизации системы неизвестен, однако можно оценить учитывая частоту ШИМ 5 КГц, частоту работы микроконтроллера 72 МГц и учитывая быстродействие остальных элементов системы можно принять T = 10 мс. (ps тут нужно сделать период меньше – 4.5кГц)

Получим дискретную передаточную функцию системы коррекции. Которая будет реализована на микроконтроллере. Формировать управляющий сигнал будем в виде прямоугольных импульсов. Для этого используем экстраполятор нулевого порядка.

При помощи программы MatLab получим дискретную передаточную функцию корректирующего устройства системы, которое в непрерывной форме имеет вид:

| W_п (s)=(525.1(0,0057s+1)(0.01603s+1))/((0,1s+1)(0,0001616s+1)) | (36)

Используем команду c2d c периодом квантования 10 мс и одним из наиболее точных методов преобразования «tustin» и получим:

| W_п ^(*) (z)=(218*z^2 -128.6*z+7.479)/(z^2 +0.03262 z - 0.8481) W_korr_discrete = 218 z^2 - 128.6 z + 7.479 ------------------------- z^2 + 0.03262 z - 0.8481 | (37)

Далее перейдем к разностному уравнению, которое будет реализовано на МК.

| W_п ^(*) (z)=(X^(*) (z))/(G^(*) (z))=(218*z^2 -128.6*z+7.479)/(z^2 +0.03262 z - 0.8481)⇔ ⇔X^(*) (z)⋅(z^2 +0.03262 z - 0.8481)= =G^(*) (z)⋅(218*z^2 -128.6*z+7.479) x[n+2]+0,03262x[n+1]-0,8481x[n]= =218[n+2]-128.6g[n+1]+7.479g[n] | (38) (39)

В итоге получили разностное уравнение, которое можно реализовать в МК.

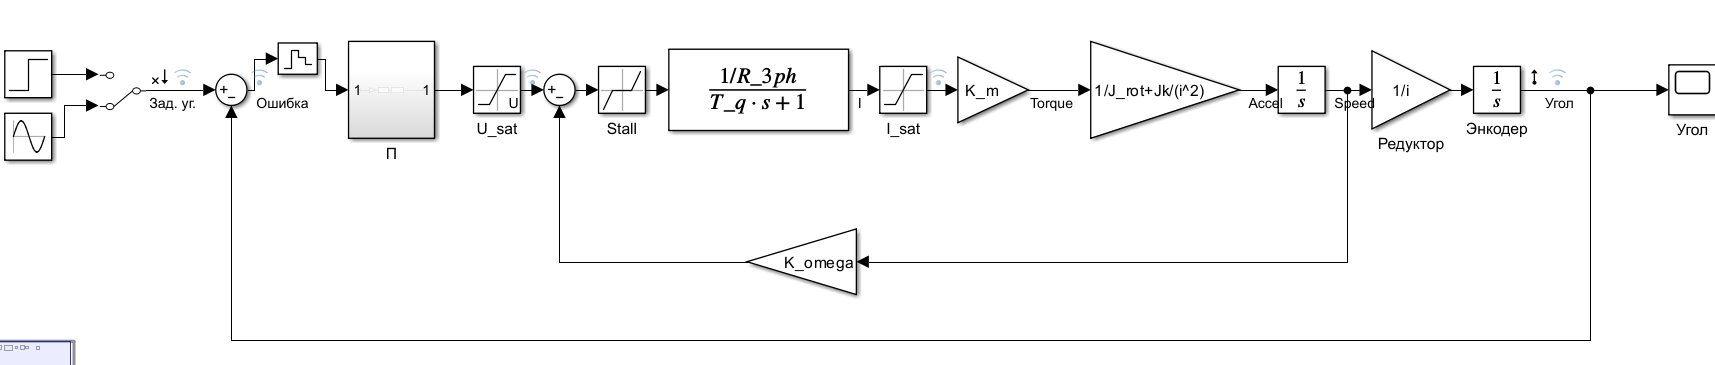
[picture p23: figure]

Для моделирования системы поставим в корректирующее устройство экстраполятор нулевого порядка (рис. 19).

Рис. 19 Дискретная система

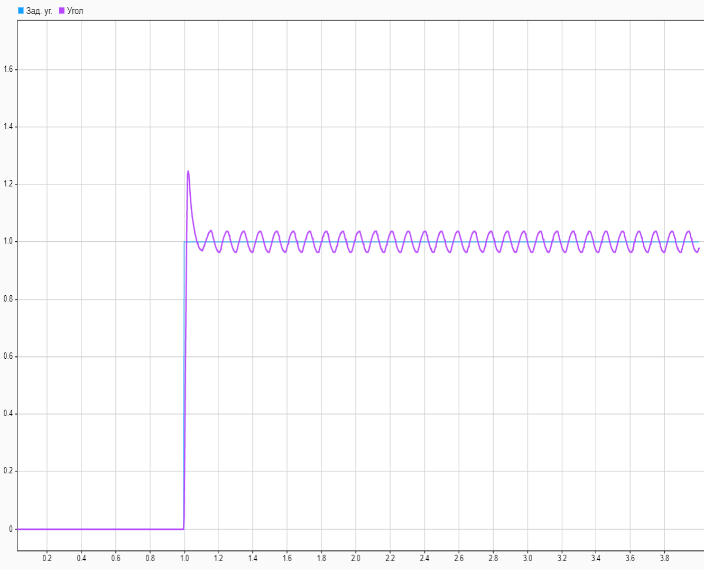
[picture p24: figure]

Посмотрим реакцию системы в следящем режиме и в режиме переброски (рис.20):

Рис. 20 Задающий и итоговый угол в 2х режимах

Как можно заметить в системе возникают колебания что вызвано дискретизацией управляющей сигнала. Т.е. система оказывается разомкнутой на протяжении периода дискретизации. Анализируя графики можно сделать вывод о том что система устойчива в заданных режимах работы.

# 6. Построение трехфазной модели BLDC двигателя и создание структурированной модели системы


Для дальнейшего развития проекта движения в сторону физической реализации, можно поэкспериментировать с моделью системы. В начале обсуждалась эквивалентная модель двигателя MX2210KV360HA на основе ДПТ. Создадим трехфазную модель двигателя (рис. 21):

Рис. 21Трехфазная модель BLDC MX2210KV360HA


Проведем некоторые тесты построенной модели, для этого подадим управляющий сигнал в виде 3 синусоид смещенных на 120 градусов каждая. Полученные графики представлены на рис. 22.

Рис. 22 Графики управляющего воздействия и скорости

Как видно из графиков, модель получилась устойчивой, однако итоговые характеристики, например скорость не сходится реальной, поэтому модель требует доработки.


Создадим общую модель системы с учетом выбранных микроконтроллера и усилителя мощности, энкодера, датчиков холла.

Рис. 23 Общая модель системы с учетом выбранных компонентов

В качестве корректирующего устройства в данной модели используется ПИД-регулятор (рис. 24)

Рис. 24 Корректирующее устройство – ПИД регулятор

Коэффициенты были подобраны с помощью Control System Tuner

Листинг 2 Код матлаб для ПИД-регулятора

% Высокоуровневый контроллер с ПИД-регулятором

kpp = 0.51624;

kip = 5.1624e-08;

kdp = 0;

kpid = 1;


Посмотрим графики в режиме слежения и переброски – рисунки 25,26

Рис. 25 Сигнал ошибки в режиме слежения (в градусах)


Рис. 26 Режим переброски

Как можно заметить из графиков, данная система справляется также хорошо с заданными режимами работы, что делает внедрение ПИД регулятора привлекательной перспективой

# ЗАКЛЮЧЕНИЕ

В процессе работы была получена модель BLDC двигателя и общая модель системы. Был проведен энергетический расчет для проверки правильности выбора двигателя.

Расчёт и моделирование были произведены в программном пакете MatLab и Simulink. Путём моделирования было установлено, что система не выполняет требуемые режимы работы. Для реализации требуемых параметров был проведён частотный синтез системы и получено корректирующее устройство, которое было дополнено нелинейными корректирующими элементами. При повторном моделировании был сделан вывод о корректности работы введённых корректирующих устройств. А также была получена дискретная модель системы, реализуемая на МК. Был сделан вывод об устойчивости итоговой дискретной модели. Также была создана модель трехфазного двигателя для дальнейших экспериментов, и структурированная модель привода оси с ПИД-регулятором, был сделан вывод о возможности такого корректирующего устройства.

# СПИСОК ИСПОЛЬЗОВАННЫХ ИСТОЧНИКОВ

1) Ротхаммель К. Энциклопедия антенн: Antennenbuch под ред. Кришке А. Изд. 11-е: Издательство ДМК-Пресс 2016. 812с. ISBN 978-5-97060-217-1

2) Биард Рэндал У., МакЛэйн Тимоти У. Малые беспилотные летательные аппараты: теория и практика 2012. 309 с.

3) C.В. Овсянников, А.А. Бошляков, А.О. Кузьмина ЭКСПЕРИМЕНТАЛЬНЫЕ ИССЛЕДОВАНИЯ В МЕХАТРОННЫХ СИСТЕМАХ

8) К.О. Коровин , С.В. Кузьмин, Реализация канала связи с БПЛА с использованием широкополосных малоэлементных антенных решеток в качестве бортовых антенных систем, 2020, 6 с.

9) Попов Е.П. Теория линейных систем автоматического регулирования и управления: Учеб. Пособие для втузов. – 2-е изд., перераб. и доп. – М.: Наука. Гл. ред. физ.-мат. лит., 1989. – 304 с.

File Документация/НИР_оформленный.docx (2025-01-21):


| Министерство науки и высшего образования Российской Федерации Федеральное государственное бюджетное образовательное учреждение высшего образования «Московский государственный технический университет имени Н.Э. Баумана (национальный исследовательский университет)» (МГТУ им. Н.Э. Баумана)

ФАКУЛЬТЕТ «Специальное машиностроение»

КАФЕДРА «Робототехнические системы и мехатроника»

РАСЧЕТНО-ПОЯСНИТЕЛЬНАЯ ЗАПИСКА

К НАУЧНО-ИССЛЕДОВАТЕЛЬСКОЙ РАБОТЕ

НА ТЕМУ:

Разработка двухосевого привода направленной антенны для установки на БПЛА

Студент СМ7-72Б _________________ Санников А.К.

(Группа) (Подпись, дата) (И.О.Фамилия)

Руководитель _________________ Гуляев И.А.

(Подпись, дата) (И.О.Фамилия)

Консультант _________________ ____________________

(Подпись, дата) (И.О.Фамилия)

2024 г.

Министерство науки и высшего образования Российской Федерации

Федеральное государственное бюджетное образовательное учреждение

высшего образования

«Московский государственный технический университет имени Н.Э. Баумана

(национальный исследовательский университет)»

(МГТУ им. Н.Э. Баумана)

УТВЕРЖДАЮ

Заведующий кафедрой __________

(Индекс)

______________ _______________

(И.О.Фамилия)

« _____ » ____________ 20 ____ г.

ЗАДАНИЕ

на выполнение научно-исследовательской работы

По теме: | Разработка двухосевого привода направленной антенны

для установки на БПЛА

Студент группы ____СМ7-72б___________

_________________________Санников Артём Константинович__________________________

(Фамилия, имя, отчество)

Направленность НИР (учебная, исследовательская, практическая, производственная, др.)

________практическая____________________________________________________________

Источник тематики (кафедра, предприятие, НИР) _____________________________________

График выполнения НИР: 25% к 5 нед., 50% к 7 нед., 75% к 10 нед., 100% к 14 нед.

Техническое задание | Разработать двухосевой привод для встраивания в систему

ретрансляции сигнала с возможностью установки на БПЛА для увеличения дальности

передачи сигнала

Оформление научно-исследовательской работы:

Расчетно-пояснительная записка на _____ листах формата А4.

Перечень графического (иллюстративного) материала (чертежи, плакаты, слайды и т.п.)

_______________________________________________________________________________

_______________________________________________________________________________

_______________________________________________________________________________

Дата выдачи задания « 17 » сентября 2024 г.

Руководитель НИР _________________ Гуляев И.А.

(Подпись, дата) (И.О.Фамилия)

Студент _________________ Санников А.К.

(Подпись, дата) (И.О.Фамилия)

Примечание: Задание оформляется в двух экземплярах: один выдается студенту, второй хранится на кафедре.

# РЕФЕРАТ

Расчетно-пояснительная записка 27 с. 17 рис., 3 табл., 8 источников.

ДВУХОСЕВОЙ ПРИВОД, БПЛА, НАПРАВЛЕННЫЕ АНТЕННЫ, РЕТРАНСЛЯТОР, РАЗРАБОТКА ПРИВОДА.

Объектом разработки является двухосевой привод направленной антенны.

Цель работы – разработка части системы ретрансляции сигнала для установки на БПЛА для увеличения дальности передачи сигнала.

Поставленная цель достигается за счет разработки двухосевого привода, направляющего антенну ретранслятора с необходимой точностью и с необходимым быстродействием, и установки данной системы на дополнительный БПЛА.

СОДЕРЖАНИЕ

# ВВЕДЕНИЕ

В настоящее время все чаще используются беспилотные летательные аппараты с FPV системами, как в исследовательских и разведывательных целях, так и в боевых условиях. Всё чаще возникает потребность в увеличении дальности работы, но при этом остается условие сохранять высокие скорости передачи данных. Решение задачи увеличения дальности передачи сигнала возможно за счёт установки ретранслятора с усилителем и на управляемом подвесе на вспомогательный БПЛА.

# 1 ОПИСАНИЕ СИСТЕМЫ И ПОСТАНОВКА ЗАДАЧИ

Для достижения значительного увеличения дальности разрабатывается система ретрансляции управляющего сигнала и видеосигнала. Предполагается, что использование дополнительного БПЛА между оператором и FPV летательным аппаратом увеличит дальность полета, при этом уделяется внимание использованию направленных антенн, и их позиционирование при помощи следящего привода, используя как входные данные уровень сигнала - RSSI (Received Signal Strength Indicator). Концепт системы на рис. 1.


Рис. 1 Концепт системы ретрансляции

При этом на дрон ретранслятор устанавливается 2 антенны, одна из которых остается неподвижной и направляется при помощи поворота дрона, а вторая устанавливается на двухосевой привод, который в свою очередь направляет антенну на FPV-дрон.

В рамках данного проекта ставится техническое задание на разработку только части системы – двухосевого привода антенны, и выбор компонетов системы: антенн и тд.

## 1.1 Описание функционала устройства

Разрабатываемое устройство представляет из себя – подвесной модуль для мультикоптерных БПЛА, с двумя направленными антеннами, одна из которых остается неподвижной относительно корпуса БПЛА и направляется при помощи вращения самого БПЛА. При этом вторая антенна приводится в движение с помощью разрабатываемого двухосевого привода.

БПЛА с установленным устройством входит в состав системы ретрансляции сигнала, также стоит отметить, что антенны будут использовать разные частоты.

## 1.2 Сферы применения

Данная система позволяет увеличивать дальность полетов, что будет очень полезно для применения в боевых условиях, а также для разведывательных и исследовательских целей, везде где требуется большая дальность и сохранение FPV функций.

## 1.3 Актуальность и новизна

Существуют двухосевые подвесы-стабилизаторы для аэрофотосъемки, также существуют дроны-ретрансляторы с двумя неподвижными антеннами широкой направленности. По сути новизна заключается в объединении этих двух идей, с целью увеличения дальности полета и повышении эффективности ретрансляции.

Основная актуальность работы – применение в боевых условиях. Так как в таких условиях наиболее важна дальность передачи сигнала.

# 2 ОБЗОР СУЩЕСТВУЮЩИХ РЕШЕНИЙ

На данный момент существуют решения: дроны-ретрансляторы с двумя неподвижными антеннами. Однако данные решения не являются прямыми аналогами системы. Один из таких устройств представлен на рис. 2.

У дрона-ретранслятора «Удлинитель» из комплекса «Упырь» увеличилась дальность полета

Рис. 2 Дрон ретранслятор

Данные системы собираются путем навесного монтажа из подручных устройств, что сказывается на надежности, однако это лишь малая часть проблемы, ведь эффективная ретрансляция сигнала, ввиду статичного расположения направленных антенн, достигается только в случае когда дрон ретранслятор находится строго между оператором и FPV-дроном. А широкая направленность позволяет в лучшем случае достигать увеличения дальности всего в 2 раза. Использование же узконаправленной антенны и правильное позиционирование в течение всего полета позволит увеличивать дальность не менее чем в 2.5-3 раза. Наглядное сравнение диаграмм направленности узконаправленной антенны и широко направленных представлено на рис. 3.

Антенна направленная Yagi 2.4/5.8 ГГц 16dBi AOSIYANT, SMA-male: продажа, цена в Днепре. Антенны беспроводных сетей от "ПО СПЕЦАНТЕНИ Зв'язок без перешкод!" - 1913079975

Рис. 3. Сравнение диаграмм направленности узконаправленной антенны и широко направленных

## 2.1 Косвенные аналоги

Рассматривая аналоги привода можно рассмотреть как косвенные аналоги – подвесы-стабилизаторы для аэрофотосъемки, стационарные приводы антенн.

Что касается подвесов для фото, один из таких представлен на рис. 4:


Рис. 4 3-х осевой подвес камеры для аэрофотосъемки.

Подобные системы имеют неподходящую кинематику, так как все они направлены в первую очередь на позиционирование камеры, и в конкретно трёхосевом варианте 3я ось предназначена для вращения камеры по горизонту. А диаграмма направленности антенны имеет форму тела вращения, и ее вращение уже неактуально. Стоит также отметить, что и характеристики по быстродействию и точности не удовлетворяют, не говоря уже о системе упраления, всё это является следствием того факта, что предназначение этого подвеса совсем другое. В добавок ко всем вышесказанному добавляется дороговизна таких устройств. Существуют и двухосевые подвесы, но в данных устройствах убирают вертикальную ось вращения и камера остается направленной по курсу БПЛА, что опять же недопустимо для наших целей.

## 2.2 Патентный поиск

По контекстным запросам:

- «Разработка двухосевого привода направленной антенны для установки на БПЛА»
- «two-axis drive of directional antenna for UAV. UAV is equipped with device with 2-axis drive and directional antenna, using stepper motors directs antenna.»,
- « двухосевой привод направленной антенны для бпла с для увеличения дальности полетов на бпла устанавливается устройство с 2 осевым приводом, и направленной антенной, с помощью шаговых двигателей направляет антенну.»

Отсутствуют релевантные результаты.

# 3 ОПРЕДЕЛЕНИЕ ПРИГОДНЫХ ТИПОВ И РАЗМЕРОВ БПЛА

Основным критерием для БПЛА является грузоподъемность и габариты. Сверхмалые и малые типоразмеры сразу отпадают ввиду низкой грузоподъемности и сложности разработки привода, ориентируемся на средние и тяжелые БПЛА мультикоптерного типа, грузоподъемностью от 1 кг и размерами от 300мм в диаметре.

Подробная классификация типов по грузоподъемности представлена в таблице 1:

Таблица 1. Сравнение типов и размеров БПЛА

Типоразмер БПЛА | Масса | Грузо-сть | Габариты в диаметр | Время полета | Макс.Высота полета
Микро-класс | До 50 гр. | 10 гр. | До 100 мм | 3-10 мин. | 10 м
Мини-класс | До 500 гр. | 100 гр. | До 250 мм. | 5-20 мин. | 100 м
Средний класс | До 2.5 кг. | 500 гр. | 350-500 мм | 30 мин. | 1000 м
Тяжелый класс | От 2.5 кг. | От 1 кг. | От 550 мм | От 50 мин. | От 1000 м

Для прототипа предприятием заказчиком был выбран квадрокоптер тяжелого класса: DJI MATRICE 300, его характеристики можно брать за основу при проектировании привода, внешний вид представлен на рис. 5.


Рис. 5. Квадрокоптер DJI MATRICE 300

# 4 ФУНКЦИОНАЛЬНАЯ СХЕМА РАЗРАБАТЫВАЕМОГО УСТРОЙСТВА

Для определения структуры устройства создадим функциональную схему. В данной научно-исследовательской работе рассматривается разработка одной из частей системы – часть на рис. 6 начиная с микроконтроллера и ниже.


Рис. 6 Функциональная схема устройства

# 5 ФОРМИРОВАНИЕ ТРЕБОВАНИЙ К ПРИВОДУ АНТЕННЫ

Исходя из структурной схемы можно понять, что объектом управления в данном приводе будет являться антенна, а вторая ось вращения зависит от первой оси. Наиболее нагруженной будет первая ось так как она будет приводить в движение подвешенную вторую ось и объект управления.

## 5.1 Требования к точности

Требования к точности можно построить исходя из диаграмм направленности антенн, которые будут использоваться. На данный момент предполагается использование направленной антенны типа yagi у которой главный лепесток и наибольшее усиление проявляется на ширине ±10°. Сечение диаграммы направленности изображено на рис. 7.

Двухдиапазонная антенна yagi в корпусе для диапазона 900 и 1800 МГц

Рис. 7 Сечение диаграммы направленности антенны.

Так как диаграмма направленности является симметричным телом вращения, логично определить что для каждой из двух осей отклонение должно быть в пределах ±10°. При этом стоит также отметить то что вторая ось висит от первой и отклонения могут складываться.

Как можно видеть на рис. 6 чем ближе к оси тем лучше усиление сигнала, поэтому учитывая эти 2 фактора стоит поставить в требования точности позиционирования антенны ±1° на каждую из двух осей.

## 5.2 Требования к быстродействию

Данную часть требований возможно поставить исходя из технических характеристик выбранного квадрокоптера, так как следящем режиме привод должен иметь возможность передвигаться быстрее квадрокоптера носителя для обеспечения бесперебойного сигнала. К тому же, забегая вперед, ввиду конструктивных возможностей, а именно ограниченного диапазона вращения, в процессе работы привода могут возникать режимы переброски. В такой ситуации быстродействие особенно важно.

Обратимся к техническим характеристикам выбранного БПЛА на рис. 8:


Рис.8 Отрывок из технических характеристик.

Минимальные угловые скорости в таком случае можно установить для первой оси - 100°/с, а для второй оси – 300 °/с.

Расчитаем ускорения, для этого построим график скоростей осей во время предполагаемого переходного процесса. Поворот на 720 градусов по техническому заданию должен занимать 0.25 сек. Примем при этом максимальную скорость оси 5000 °/с. Результаты представлены на рис. 9 и в листинге 1:


Рис. 9 Графики Скорости и Ускорения

clc

clear all

close all

t0 = 0; W0 = 0;

W_max = 5000 % Максимальная скорость оси

t_max = 0.25; % Максимальное время процесса

t1 = 2*t_max/5;

t2 = 3*t_max/5;

E_max = (W_max - W0)/(t1-t0) % Максимальное ускорение оси

t = [t0 t1 t2 t_max ];

W = [W0 W_max W_max W0 ];

E = [E_max E_max 0 0 -E_max -E_max];

t_e = [t0 t1 t1 t2 t2 t_max ];

S = (t_max+(t_max/3))*W_max/2 %пройденный путь в градусах, по тз = 720

%---------------График скоростей---------------------

figure;

plot(t, W, 'LineWidth',2, 'color', 'blue')

xlim([0 t_max*1.5]);

ylim([0 W_max+W_max/3]);

title('Скорость осей');

grid on;

xlabel('Время, Сек.') ;

ylabel('Угловая скорсоть, °/сек ');

legend({'ω','Second curve'},'Location','northeast')

%----------------------------------------------------

%---------------График ускорений---------------------

figure;

plot(t_e, E, 'LineWidth',2, 'color', 'red')

xlim([0 t_max*1.5]);

ylim([-(E_max+E_max/3) E_max+E_max/3]);

title('Ускорения осей');

grid on;

xlabel('Время, Сек.') ;

ylabel('Угловое ускорение, °/сек^2 ');

legend({'ε','Second curve'},'Location','northeast')

%----------------------------------------------------

W_max =

5000

E_max =

50000

S =

833.3333

Листинг 1. Код Matlab и вывод программы

Итого получаем требуемое уголовое ускорение:

| ε= 50000°/с^2 =872,66рад/с^2 | (1)

И угловую скорость:

| ω=5000°/с=87,26рад/с | (2)

## 5.3 Кинематическая схема привода антенны

Кинематическая схема привода антенны представлена на рисунке 10. На данной схеме представлены 2 степени свободы – ось 1 и ось 2. А также 4 системы координат: глобальная X0Y0Z0, относительно поверхности земли где ось Z0 -перпендикулярна поверхности земли, система координат XYZ привязанная к корпусу БПЛА, X1Y1Z1 система координат первой оси с вращением вокруг Z1 по углу φ, и система координат X2Y2Z2 с вращением вокруг оси X2 и X1 по углу γ.


Рис. 10 Кинематическая схема привода

При этом углы φ и γ находятся в определенных пределах:

| -180°≤γ≤0° 0°≤φ≤360° | | (3)

Данные пределы возникают исходя из задачи выполняемой устройством и особенностями конструкции. Угол φ имеет данные пределы для обеспечения возможности кругового вращения и направления антенны по всему периметру БПЛА. Угол γ определяется из тех. Требований и концепции системы, согласно которой БПЛА-ретранслятор находится на большей высоте чем FPV-БПЛА. Для обеспечения кругового обзора достаточно и ограничения общего хода в 90 ° однако для улучшения быстродействия в режиме переброски, который может возникать в предельных значениях вертикальной оси можем увеличить ограничения до 180 ° .

## 5.4 Общие требования к конструкции и грузоподъемности привода

В процессе работы привод безусловно будет сталкиваться с нагрузкой со стороны ветра, при этом в режимах работы выбранного БПЛА допускается скорость ветра до 15 м\с. В наших условиях возможно простое решение данной проблемы – установка радиопрозрачного кожуха, например из пластика. Такое решение никак не повлияет на работу системы, при этом решит проблему воздействия ветра. Соответственно одно из требований к приводу – наличие защитного кожуха.

Требование к габаритам привода также необходимо учитывать. Поскольку предполагается установка привода снизу БПЛА чем менее габаритное будет устройство тем меньше оно будет влиять на летные характеристики БПЛА. Предельные размеры до лопастей: 350х350х350мм.

Предельная общая масса привода также опирается на технические характеристики выбранного квадрокоптера. Его грузоподъемность составляет 2700 г.

Что касается грузоподъемности привода – определим требуемые моменты для привода, для этого рассчитаем момент требуемый для 1 оси так как она самая нагруженная. Для этого создадим грубую модель привода в САПР, и узнаем момент инерции.


Рис. 11 Грубая 3Д модель привода для оценки моментов инерции.

Рассчитанный момент инерции конструкции:

| I_(yy) = 748,534 кг мм^2 =7.48534*10^(-5) кг м^2 | (4)

Тогда требуемый момент на выходном валу:

| M=I_(yy) *ε=872,66*7.48534*10^(-5) =0.0653 Н*м | (5)

DJI Matrice 300 RTK Купить- Лучшая цена | Aeromotus

Рис. 12 Внешний вид и габаритные характеристики БПЛА

# 6 ПОДБОР КОМПОНЕНТОВ ДЛЯ РАЗРАБАТЫВАЕМОГО УСТРОЙСТВА

Объектом управления в данном приводе будет являться направленная антенна, поэтому необходимо для начала определиться с выбором антенны, для дальнейшего определения остальных компонентов.

## 6.1 Требования к антенне и выбор антенны

Для работы с FPV системами стоит использовать частоту: 2.4 ГГц. И выбрать направленную антенну, которая будет отличатся небольшими габаритами и малым весом. Подходящие варианты антенн представлены на рис. 13:


Рис. 13 Варианты направленных антенн для 2.4 ГГц

## 6.2 Выбор типа двигателей для привода

Рассмотрим 3 варианта двигателей, которые можно поставить в разрабатываемое устройство - их преимущества и недостатки в рамках данной задачи:

1) Шаговые двигатели: к преимуществам можно отнести возможность отслеживать угол поворота и более точно позиционировать вал, однако для нашей системы ввиду высоких требований к быстродействию шаговые двигатели не подходят.

2) Двигатель постоянного тока: весьма простое и удобное решение, однако по аналогии с шаговым будет трудно найти двигатель с достаточно большой скоростью вращения для удовлетворений требований быстродействия.

3) Синхронный двигатель с постоянными магнитами, или же BLDC двигатель: данный вариант кажется наиболее подходящим, так как легко найти двигатели с достаточной скоростью вращения, к тому же для задач слежения за положением лучше подходит BLDC чем ДПТ.

Таким образом лучше всего для разрабатываемого устройства подходит синхронный двигатель с постоянными магнитами.

## 6.3 Выбор двигателей для привода редукторов и энкодеров

Для начала выберем двигатель для первой оси и подберем редуктор, выбранный двигатель будем использовать и на второй оси. В данном случае электрический двигатель может быть подобран по требуемой мощности, исходя из условия:

| P_(дв) ≥(P_(дв) )_р ; (Р_(дв) )_р =ξ(P_н)/(η_0) . | (6)

Мощность на выходном валу (мощность нагрузки):

| Pн = М ∙ ω =0.0653*87,26= 5.69 Вт | (7)

По характеру работы привода можно принять:

| ξ = 1.2 | (8)

Тогда расчётная величина, требуемой от двигателя мощности будет:

| (Р_(дв) )_р =ξ(P_н)/(η_0)=1.25.69/0.6=11.38 Вт | (9)

(коэффициент потерь η_0 примем равным 0.6)

Выбираем BLDC двигатель MX2210KV360HA с планетарным редуктором и передаточным отношением 3.3.


Рис. 14 Строение мотора-редуктора


Рис. 15 Характеристики мотора и редуктора.


Рис. 16 Характеристики мотора MX2210KV360HA

Запишем необходимые характеристики в таблицу:

Таблица 2. Характеристики двигателя и редуктора

Характеристика | Значение | Ед. измерения
Номинальные обороты | 3300 | Об/мин
Номинальный момент | 0.033 | Н*м
Момент страгивания | 0.105 | Н*м
Момент инерции ротора | 0.00000076 | Кг м²
Индуктивность обмотки | 100 | мкГн
Сопротивление обмотки | 750 | мОм
Номинальное напряжение | 12 | В
Передаточное отношение редуктора | 3.3 | -
Количество полюсов | 7 | -
KV | 360 | -
Постоянная момента | 0.023 | Н*м/А

Подберем подходящий энкодер исходя из требований к точности и габаритам подберем энкодер небольших размеров и разрешением 4096 импульсов:


Рис. 17 Энкодер ACCNT

# ЗАКЛЮЧЕНИЕ

В заключение работы, обобщим краткое техническое задание на разработку двухосевого привода.

Таблица 3. Техническое задание на разработку привода

Параметр | Значение | Ед. измерения
Общая масса | 2700 | г.
Предельные габариты | 300х300х300 | мм
Напряжение питания | 12 | В
Диапазон вращения оси 1 | 0≤φ≤360 | °
Диапазон вращения оси 2 | -180≤γ≤0 | °
Угловая скорость вращения осей | 87,26 | рад/с
Угловое ускорение вращения осей | 872,66 | рад/с ²
Время переброски на 360° (время переходного процесса) | 0.125 | сек
Ошибка слежения | 1 | °
Перерегулирование при переброске | 25 | %

# СПИСОК ИСПОЛЬЗОВАННЫХ ИСТОЧНИКОВ

1) Ротхаммель К. Энциклопедия антенн: Antennenbuch под ред. Кришке А. Изд. 11-е: Издательство ДМК-Пресс 2016. 812с. ISBN 978-5-97060-217-1

2) Биард Рэндал У., МакЛэйн Тимоти У. Малые беспилотные летательные аппараты: теория и практика 2012. 309 с.

3) C.В. Овсянников, А.А. Бошляков, А.О. Кузьмина ЭКСПЕРИМЕНТАЛЬНЫЕ ИССЛЕДОВАНИЯ В МЕХАТРОННЫХ СИСТЕМАХ

4) DJI LLC Краткое руководство пользователя DJI MATRICE 300 2015. 109 с.

5) Кокорев Ю.А., Жаров В.А., Торгов А.М. Расчет электромеханического привода: Учеб. пособие Под ред. В.Н.Баранова. — М.: Изд-во МГТУ, І995. 132 с

6) А.И. Еремеев и др.; Под. ред. О.Ф. Тищенко. А 1. тлас конструкций элементов приборных устройств: Учеб. Пособие для студентов приборостроительных специальностей ВУЗов /А.А. Буцев, М.: Машиностроение, 1982. 116с.

7) М. Г. Алешин, С. В. Дьяконов, А. Ю. Сивов, ОБОСНОВАНИЕ ОСНОВНЫХ ХАРАКТЕРИСТИК АНТЕННОЙ СИСТЕМЫ И ПАРАМЕТРОВ УПРАВЛЕНИЯ МОЩНОСТЬЮ ПЕРЕДАТЧИКА РЕТРАНСЛЯТОРА СВЯЗИ НА БЕСПИЛОТНОМ ЛЕТАТЕЛЬНОМ АППАРАТЕ 2011. 21 c.

8) К.О. Коровин , С.В. Кузьмин, Реализация канала связи с БПЛА с использованием широкополосных малоэлементных антенных решеток в качестве бортовых антенных систем, 2020, 6 с.

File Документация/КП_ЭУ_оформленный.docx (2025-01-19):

| Министерство науки и высшего образования Российской Федерации Федеральное государственное бюджетное образовательное учреждение высшего образования «Московский государственный технический университет имени Н.Э. Баумана (национальный исследовательский университет)» (МГТУ им. Н.Э. Баумана)

ФАКУЛЬТЕТ «Специальное машиностроение»

КАФЕДРА «Робототехнические системы и мехатроника»

РАСЧЕТНО-ПОЯСНИТЕЛЬНАЯ ЗАПИСКА

К КУРСОВОМУ ПРОЕКТУ

НА ТЕМУ:

Разработка двухосевого привода направленной антенны для установки на БПЛА

Студент СМ7-72Б _________________ Санников А.К.

(Группа) (Подпись, дата) (И.О.Фамилия)

Руководитель _________________ Гуляев И.А.

(Подпись, дата) (И.О.Фамилия)

Консультант _________________ ____________________

(Подпись, дата) (И.О.Фамилия)

2024 г.

Министерство науки и высшего образования Российской Федерации

Федеральное государственное бюджетное образовательное учреждение

высшего образования

«Московский государственный технический университет имени Н.Э. Баумана

(национальный исследовательский университет)»

(МГТУ им. Н.Э. Баумана)

УТВЕРЖДАЮ

Заведующий кафедрой __________

(Индекс)

______________ _______________

(И.О.Фамилия)

« _____ » ____________ 20 ____ г.

ЗАДАНИЕ

на выполнение курсового проекта

По теме: | Разработка двухосевого привода направленной антенны

для установки на БПЛА

Студент группы ____СМ7-72б___________

_________________________Санников Артём Константинович__________________________

(Фамилия, имя, отчество)

Направленность КП (учебная, исследовательская, практическая, производственная, др.)

________практическая____________________________________________________________

Источник тематики (кафедра, предприятие, НИР) ____НИР______________________________

График выполнения КП: 25% к 5 нед., 50% к 7 нед., 75% к 10 нед., 100% к 14 нед.

Техническое задание | Разработать блок управления двухосевого привода для

встраивания в систему ретрансляции сигнала с возможностью установки на БПЛА

для увеличения дальности передачи сигнала

Оформление курсового проекта:

Расчетно-пояснительная записка на _____ листах формата А4.

Перечень графического (иллюстративного) материала (чертежи, плакаты, слайды и т.п.)

_______________________________________________________________________________

_______________________________________________________________________________

_______________________________________________________________________________

Дата выдачи задания « 17 » сентября 2024 г.

Руководитель КП _________________ Гуляев И.А.

(Подпись, дата) (И.О.Фамилия)

Студент _________________ Санников А.К.

(Подпись, дата) (И.О.Фамилия)

Примечание: Задание оформляется в двух экземплярах: один выдается студенту, второй хранится на кафедре.

СОДЕРЖАНИЕ

# ВВЕДЕНИЕ

В последние годы беспилотные летательные аппараты (БПЛА) с системами FPV (First-Person View) становятся всё более популярными. Эти технологии находят широкое применение в различных областях, включая исследования, разведку и даже боевые действия. Одним из важнейших аспектов, который определяет эффективность использования БПЛА, является дальность передачи сигнала. Однако с увеличением дальности работы возникает проблема обеспечения стабильности и скорости передачи данных, что критично для успешного функционирования таких аппаратов в различных условиях.

Для решения этой задачи разрабатывается привод направленной антенны ретранслятора для установки на вспомогательный БПЛА. Это позволяет значительно увеличить дальность действия системы без потери качества передачи данных. В данном контексте создание эффективных систем управления для таких комплексов становится ключевым элементом для успешного функционирования всей системы в целом.

В рамках настоящей курсовой работы, опираясь на курсовую работу по теории автоматического управления (ТАУ), будет разработан блок управления для двух BLDC двигателей, предназначенный для управления подвесом ретранслятора на вспомогательном БПЛА. Этот блок управления обеспечит точную настройку и стабилизацию работы системы, что в свою очередь повысит эффективность работы всей системы ретрансляции и передачи данных на больших расстояниях.

# 1 Техническое задание

Необходимо разработать плату для управления двумя двигателями привода, с входным интерфейсом для приема управляющих воздействий, которые будут приходить в формате 2х требуемых углов поворота.

В ходе научно-исследовательской работы было определены требуемые характеристики привода:

Таблица 1. Техническое задание на разработку привода

Параметр | Значение | Ед. измерения
Общая масса | 2700 | г.
Предельные габариты | 300х300х300 | мм
Напряжение питания | 12 | В
Диапазон вращения оси 1 | 0≤φ≤360 | °
Диапазон вращения оси 2 | -180≤γ≤0 | °
Угловая скорость вращения осей | 87,26 | рад/с
Угловое ускорение вращения осей | 872,66 | рад/с ²
Время переброски на 360° (время переходного процесса) | 0.125 | сек
Ошибка слежения | 1 | °
Перерегулирование при переброске | 10 | %


Рис. 1 Кинематическая схема привода

Здесь стоит отметить что в ходе курсовой работы по ТАУ было принято решение использовать BLDC двигатели MX2210KV360HA с датчиками холла для каждой оси:


Рис. 2 BLDC двигатели MX2210KV360HA

Также были определены используемые энкодеры обратной связи на 4096 импульсов на оборот, представлен на рисунке 3:


Рис. 3 Энкодер ACCNT

Таблица 2. Параметры импульсного датчика положения

Количество импульсов на оборот | 4096
Напряжение питания, В | 5
Потребляемый ток, мА | 12
Количество сигнальных выходов | 4

Согласно которой можно определить что управляющий сигнал поступает на плату через интерфейс UART, что также важно при разработке блока управления. Дополнительно нужно реализовать интерфейс для программирования МК, и дополнительные отладочные выводы, которые будут определены в ходе разработки.

Питание платы будет осуществляться от бортового аккумулятора БПЛА, согласно документации выбранного квадракоптера DJI MATRICE 300, составлена таблица параметров источника питания:

Таблица 3. Параметры источника питания блока управления

Емкость аккумулятора, mAh | 5935
Напряжение питания, В | 12
Максимальный ток, А | 360

2. Функциональная схема блока управления


Опираясь на функциональную схему разработанную в ходе нучно исследовательской работы составим функциональную схему разрабатываемого блока управления, источник питания не учтен на схеме:

Рис. 4 Функциональная схема блока управления

Как видно из схемы система получается симметричная поэтому дальнейшие расчеты и рассуждения будем проводить лишь для одного из двигателей, второй будет получен методом копирования.

# 3 Создание блока управления двигателем

Для управления BLDC двигателем необходимо реализовать часть схемы – блок управления двигателем (усилитель мощности). Управлять таким двигателем можно реализовав векторное управление: обрабатывать сигналы с датчиков холла, генерировать управляющий трехфазный ШИМ-сигнал. Однако с программной точки зрения это непростая задача, поэтому было принято решение использовать готовые драйверы, которые уже самостоятельно решают задачу управления скоростью(см. рис 6), и на вход принимают уже только один ШИМ-сигнал и несколько логических сигналов. Примером такого модуля является – микросхема JY01(рис. 5) его мы и будем использовать в качестве основы блока управления.


Рис. 5 Контроллер JY01


Рис. 6 Осциллограмма управляющих сигналов

В документации к микросхеме[6] приведены несколько схем подключения, различных ситуаций, например схема с обратной связью по току, или по скорости. Выбираем схему с датчиками холла так как в выбранный двигатель они встроены и мы можем их использовать. Схема Подключения представлена на рис. 7.


Рис. 7 Схема подключения с датчиками Холла

Помимо самого драйвера в систему также входят драйверы ключей IR2101. Выбираем вариант в корпусе SOIC8, так как он подходит по мощности и занимает меньше места чем DIP исполнение. Типовая схема подключения представлена на рисунке 8.


Рис. 8 Схема подключения IR2101

В схеме имеются диод и конденсаторы, выберем диод IN4148WS и керамические конденсаторы номиналом 105 пФ в корпусе 0603 в соответствии с рекомендациями производителя микросхемы JY01.

## 3.1 Расчет силового каскада

В документации JY01 приведена общая структура и конкретные транзисторы для силового каскада необходимо подбирать для каждого конкретного двигателя. Решим задачу подбора транзисторов.

Выбор транзисторного ключа осуществляется по напряжению, протекаемому в цепи стока (коллектора) току, выделяемой мощности и частотным характеристикам. Для начала, получим исходные данные для расчета:

| U_(си.макс) =1.1U_(дв) =1.1*12=13.2 В | (1.1)
| I_(си.макс) =2*I_(дв.п) =2*4=8 А | (1.2)
| f_(ср.дв) =35мкс | (1.3)

Рассчитаем допустимые значение силы тока и напряжения, для этого добавим к исходным данным запас, следующим образом:

| [U_(си) ]=(U_(си.макс))/0.75=13.2/0.75=17.6 В | (1.4)
| [I_(си) ]=(I_(си.макс))/0.55=8/0.55=14.54 А | (1.5)

Выбираем транзистор, параметры которого превосходят допустимые. Предварительно берем микросхему IRF8736PBF которая является MOSFET транзистором в корпусе SO-8. C максимальным напряжением 30 В. Ее достоинством является низкое сопротивление открытого канала, что позволяет избежать разработку теплоотвода.

Согласно спецификации на эту микросхему [7], требуемый нами ток 14.54А возможен для протекания до температуры корпуса 60 градусов. График зависимости силы тока от температуры корпуса представлен на рис. 9.


Рис. 9 Зависимость тока стока от температуры корпуса

Таким образом транзистор проходит по току и по напряжению, оценим мощности. Согласно документации сопротивление открытого канала при температуре не более 60 градусов будет составлять 3.9 мОм. Тогда максимальная мощность на транзисторе будет равна

| P_(си.ст.макс) =R_(DS(on)) *I_(си.макс) ^2 =3.9*10^(-3) *8^2 =0.24 Вт | (1.6)

Для расчета динамических параметров необходимо будет определить времена переключения транзистора. Также, надо рассчитать частоту коммутации ключей. Она была определена как частота ШИМ – 4.5 кГц. Внешнее сопротивление цепи затвора возьмем из рекомендуемой схемы в документации 100 Ом.

Считаем время переключения транзистора

| t_(перекл) =C_(rss) *(R_(др) +R_(з.внеш) +R_(з.внутр) )(U_(зи.макс))/(U_(зи.макс) -U_(зи.пор))==219*10^(-12) *(10+15+34)12/(12-5)==22.15 Нс | (1.7)

Внутренне сопротивление затвора было рассчитано по той же формуле для приведенных в спецификациях параметрах. Сопротивление драйвера берется из спецификации.

Считаем динамическую мощность переключения

| P_(дин) =I_(cи.макс) *U_(си.макс) *f(t_(перекл))/2==8*13.2*4.5*10^3 *(22.15*10^(-9))/2=0.005 Вт | (1.8)

Суммарная выделяемая мощность

| P=P_(дин) +P_(ст) =0.005+0.24=0.245 Вт | (1.9)

Допускаемая выделяемая мощность равна

| [P]=P/(0.7…0.8)=0.245/0.75=0.326 Вт | (1.10)

Проверяем не перегревается ли транзистор при заданной мощности. Температуру кристалла мы можем посчитать методом термоэлектронной аналогии по формуле

| T_(кр) =T_(окр.ср) +R_(кр-окр.ср) *[P]=25+62.5*0.326=45.375 °С | (1.11)

Приведенная температура не перегревает транзистор. Таким образом можем считать что радиатор не понадобится. Обратный диод также не потребуется, достаточно внутреннего диода.

Выбранный MOSFET транзистор обладает высокими частотными свойствами. Проводить проверку по частотным характеристикам не потребуется.

## 3.2 Гальваническая развязка

Для снижения влияния помех и предотвращения ложного срабатывания драйвера, необходимо осуществить гальваническую развязку между силовой и логической цепями. Для этого могут служить оптические пары, например оптроны. Подберем их.

Итак, как было получено ранее, нам необходимо, чтобы двигатели коммутировались с частотой 4.5 кГц. Тогда получим частотные ограничения на оптроны, исходя из того, что время их включения и выключения в сумме должно

быть меньше, чем 25% длины самого короткого импульса ШИМ, который соответствует напряжению трогания двигателя:

| (t_(вкл) +t_(вкл) )=0.25*(U_(трог))/(U_(ном))1/f=0.25*1/12*1/(4.5*10^3)=4.62 мкс | (2.1)

Данному требованию удовлетворяет высокоскоростная оптопара HCPL4504-000E с транзисторным выходом. Выберем её.


Оставшиеся логические выходы работают медленнее и их можно коммутировать с помощью обычной оптопары, выберем 4-х канальную оптопару ради экономии места - TLP291-4_GB_E_T (рис. 10).

Рис. 10 4-х канальная оптопара TLP291

Далее подберем резисторы для входной и выходной цепи опторазвязки. Для начала необходимо рассчитать входную цепь. Так как оптопара представляет из себя обычный светодиод, необходимо добавить токоограничивающий резистор, в соответствии с рабочим током оптопары. Согласно документации этот рабочий ток 25 мА, напряжение микроконтроллера 3.3 В. Номинальное сопротивление резистора будет равно

| R=(U_(вх.вкл))/I=3.3/(25*10^(-3))=132 Ом | (2.2)

Выбираем ближайшее значение, по рядку Е24 берем резистор в корпусе 0603 на 130 Ом. Для 4-х канальной оптопары рабочие токи светодиодов отличаются, рассчитаем аналогично резисторы

| R=(U_(вх.вкл))/I=3.3/(50*10^(-3))=66 Ом | (2.3)

Выбираем ближайшее значение, по рядку Е24 берем резистор в корпусе 0603 на 68 Ом.

Для выходной цепи необходимо выбрать резисторы которые будут выполнять роль делителя напряжения. Согласно спецификации на драйвер на цифровых входах максимальное напряжение +5 В.

Необходимо реализовать следующий коэффициент деления

| k=(U_(цель))/(U_(пит))=5/12=0.416 | (2.4)

Предварительно берем резистор на 51 кОм. Тогда второй резистор будет

| R_2 =(R_1 k)/(1-k)=(51*0.416)/(1-0.416)=36.3 кОм | (2.5)

Округляем по ряду E24 получаем значение 36 кОм, тогда получаем напряжение

| U_(итог) =(U_(пит) *R_2)/(R_1 +R_2)=(12*36)/(51+36)=4.96 В | (2.6)

Таким образом, считаем что ошибка несущественна, берем эти номинальные значения в корпусах SMD 0603.

# 4 Выбор микроконтроллера и его подключение

Перейдем к выбору микроконтроллера для нашей системы. Перед этим, сформулируем требования, которым он должен соответствовать учитывая особенности ТЗ. Будущий микроконтроллер должен иметь:

- 2 независимых модуля ШИМ
- 4 свободных цифровых портов для выбора направления вращения и активации
- Интерфейс UART для получения команд
- 2 свободных АЦП канала для получения обратной связи по скорости
- 8 свободных портов для инкрементальных датчиков положения
- 2 модуля таймера с аппаратным счетчиком импульсов инкрементального энкодера
- I2C интерфейс для потенциального подключения IMU модуля

Также необходимо учесть, напряжение питания – 3.3 В.

Всем приведенным требованиям удовлетворяет микроконтроллер

компании STMicroelectronics модели STM32G474 [3]. Приведем его основные

характеристики в таблице 4.

Таблица 4. Основные характеристики микроконтроллера

Параметр | Характеристика
Объем флеш-памяти | 512 КБ
Объем SRAM | 96 КБ
Количество таймеров | 13 общего назначения и 4 продвинутых по 4 канала каждый
Количество АЦП | 5 12-битных до 42 каналов
Тактовая частота | 170 МГц
Напряжение питания | 2.0-3.6 В

Выбираем микроконтроллер в корпусе LQFP64, в котором предусмотрено 64 контакта из соображений дополнительного запаса.


Продумаем схему подключения микроконтроллера к плате, а также поддержки сброса микроконтроллера при необходимости. Начнем с реализации внешнего сигнала сброса. В нестандартных ситуациях может потребоваться сброс ядра микроконтроллера вручную. Для этого в схему добавим кнопку и керамический конденсатор так, как показано на рис. 11

Рис. 11. Порядок коммутации кнопки сброса

Рабочее напряжение конденсатора должно быть, согласно рисунку, не менее VDD, то есть напряжения питания микроконтроллера. Для этого подойдет конденсатор 0.1 мкФ в SMD корпусе 0603, кнопку берем 1437566-3 тоже поверхностного монтажа.

Далее реализуем схему подключения питания. Согласно документации схема питания реализуется как на рис. 12.


Рис. 12. Схема подключения питания к микроконтроллеру

Таким образом, для коммутации источника питания потребуется 5 конденсаторов на 100 нФ, 1 конденсатор на 10 нФ, 2 конденсатора на 1 мкФ и один конденсатор на 4.7 мкФ . Все их берем керамические поверхностного монтажа в корпусах 0603.

Для обеспечения функционирования МК подключим к нему внешний кварцевый резонатор с частотой 8МГц так, как показано на рис. 13.


Рис. 13. Подключение внешнего источника опорной частоты.

Выберем кварцевый резонатор модели NX5032GA для поверхностного

монтажа. Для расчета дополнительных подключаемых компонентов, воспользуемся запиской AN2867 для микроконтроллера [5].

Нагрузочная ёмкость резонатора, согласно его спецификации, составляет

8пФ. Тогда, приняв паразитную емкость проводников печатной платы, равную 2пФ, имеем необходимую емкость конденсаторов (при условии их одинаковости):

| C_(L_12) =2(C_L -C_(пар) )=2(8-2)=12 пФ | (3.1)

Таким образом, берем конденсаторы на 12 пФ корпус 0603.

Номинал внешнего резистора можно рассчитать по формуле:

| R=1/(2π*f*C_(L_12))=1/(2*π*8*10^6 *12*10^(-9))=1.65 Ом | (3.2)

Округляя по ряду Е24, получаем номинальное значение 1 Ом. Берем

резистор для поверхностного монтажа, так как ток в цепи осциллятора предельно

мал.
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

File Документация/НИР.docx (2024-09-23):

ТЕМА НИР: Разработка двухосевого привода анализатора радио-спектра для установки на БПЛА.

Сферы применения:

Установка привода на FPV и автономные БПЛА средней и тяжелой грузоподъемности, для проведения разведывательных и исследовательских полетов с целью анализа радиоэфира

Актуальность и новизна:

Существуют двухосевые подвесы-стабилизаторы для аэрофотосъемки, также на квадрокоптеры ставят анализаторы спектра, однако при установке анализатора не используется направленные антенны и приводы для вращения антенн. По сути новизна заключается в объединении этих двух идей.

Актуальность – применение в боевых условиях.
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

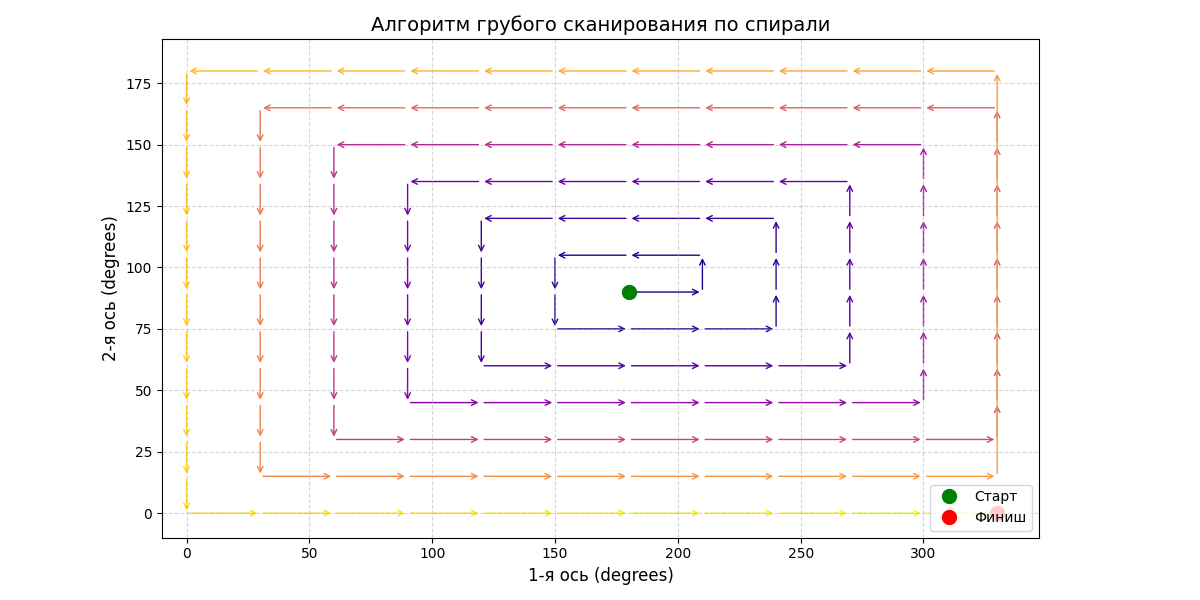
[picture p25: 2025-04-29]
Функциональные и кинематические схемы и тд/График_сканирования.png

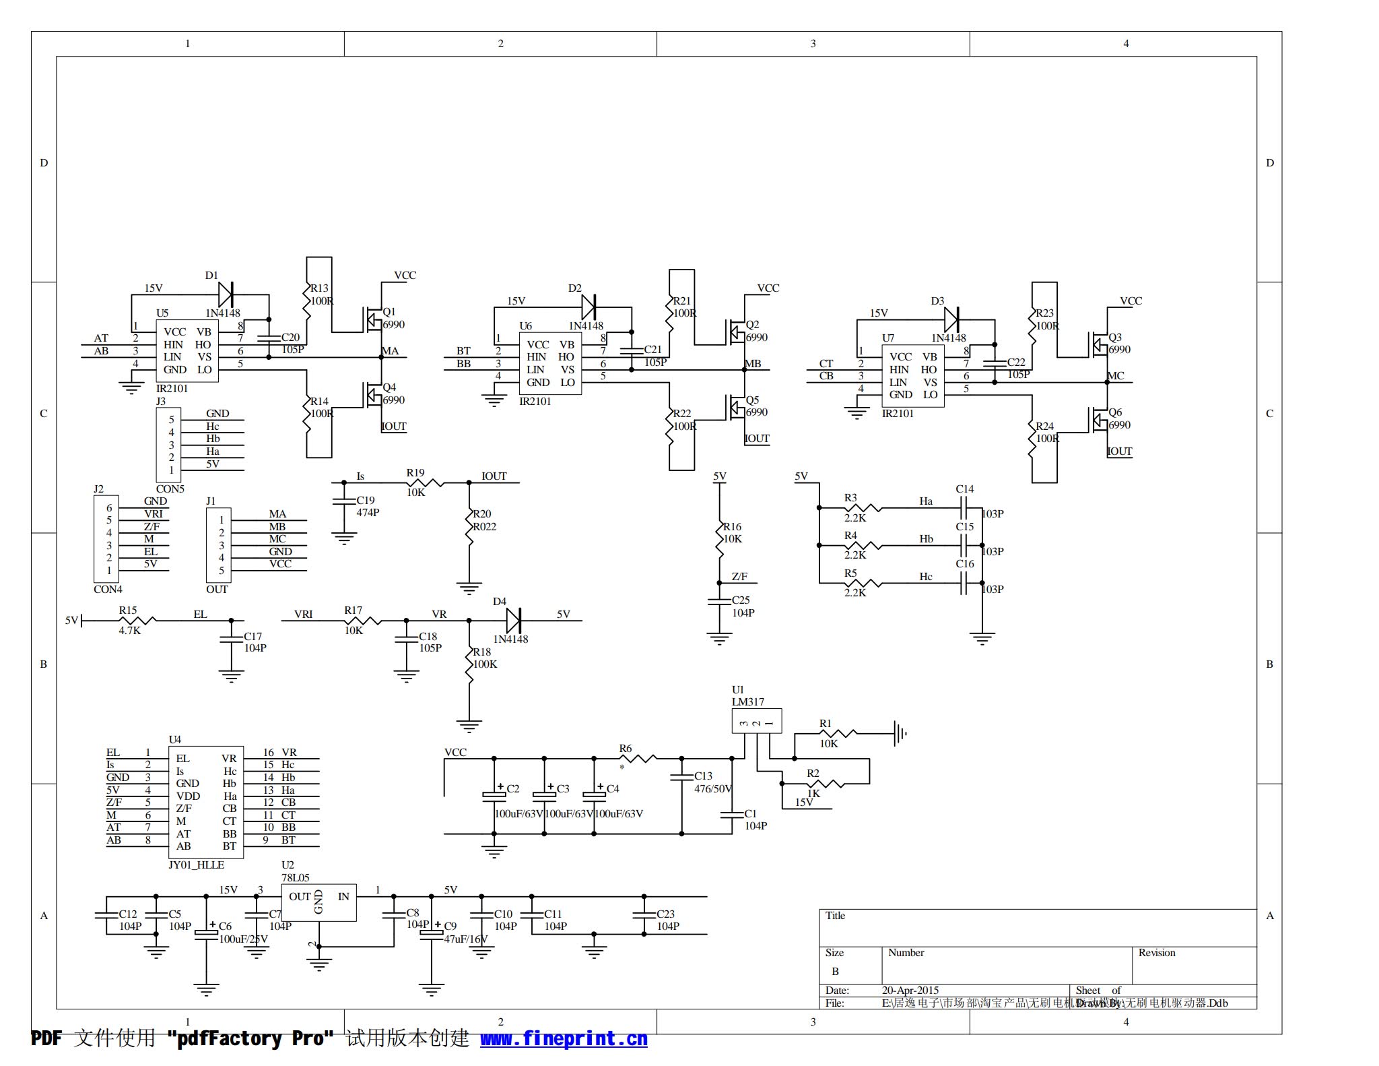
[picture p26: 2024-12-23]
Dual_BLDC_Controller/Hall_mode_JY01.png

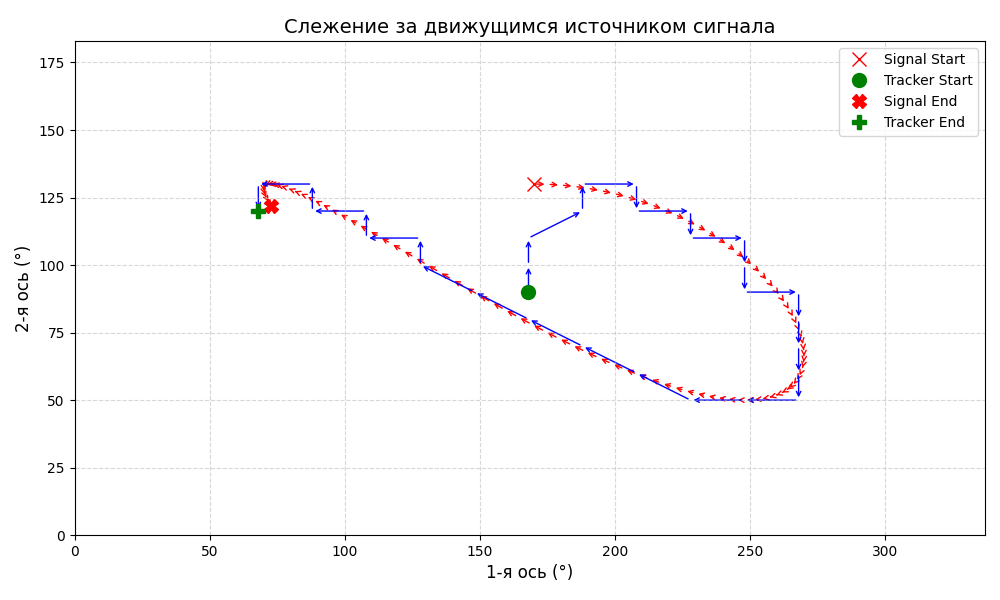
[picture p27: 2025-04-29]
Функциональные и кинематические схемы и тд/График_слежения.png

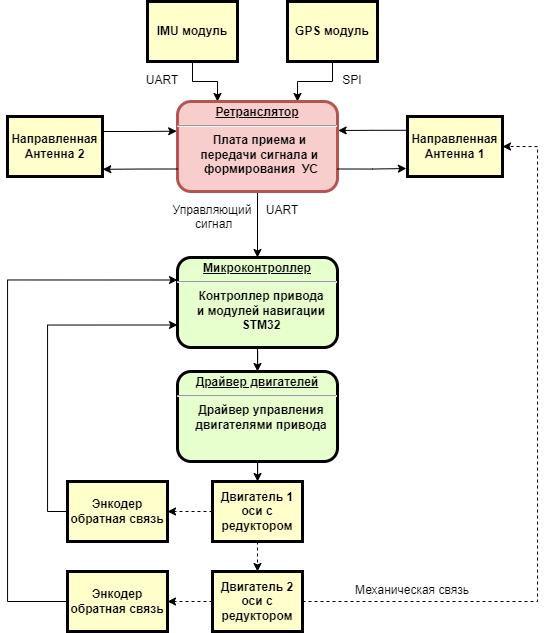
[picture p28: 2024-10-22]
Функциональные и кинематические схемы и тд/two-axis gimbal.png

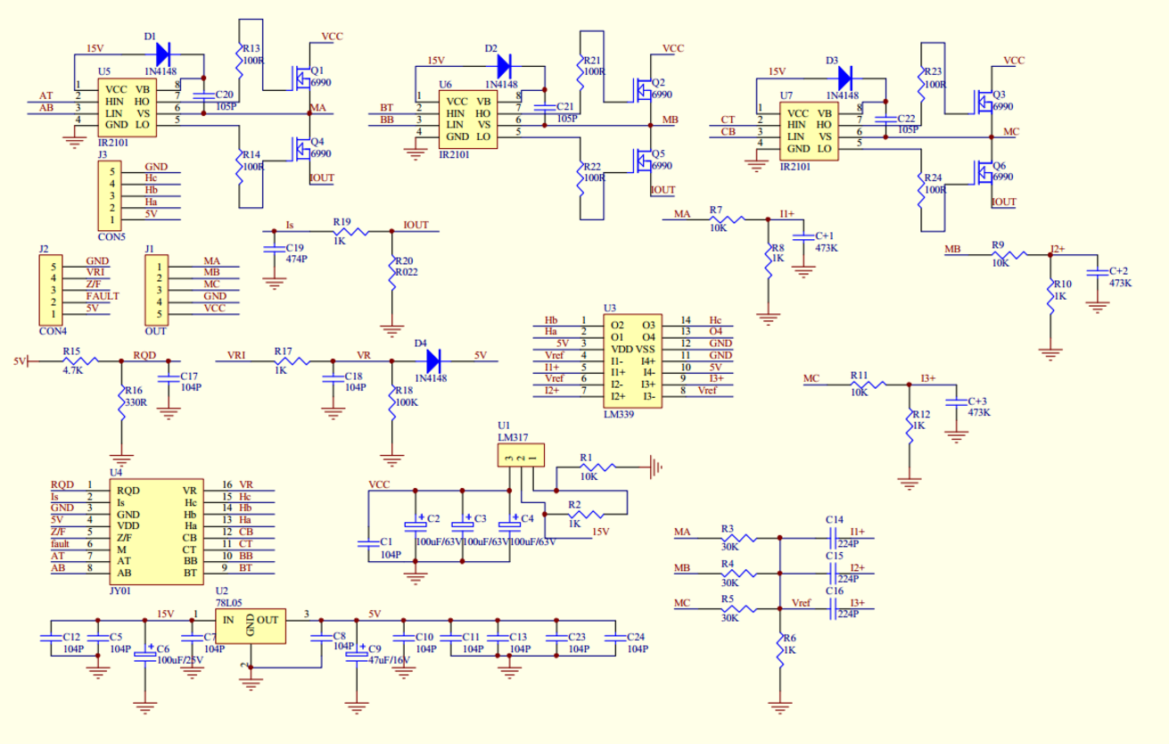
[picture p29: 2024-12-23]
Dual_BLDC_Controller/Screenshot_1.png

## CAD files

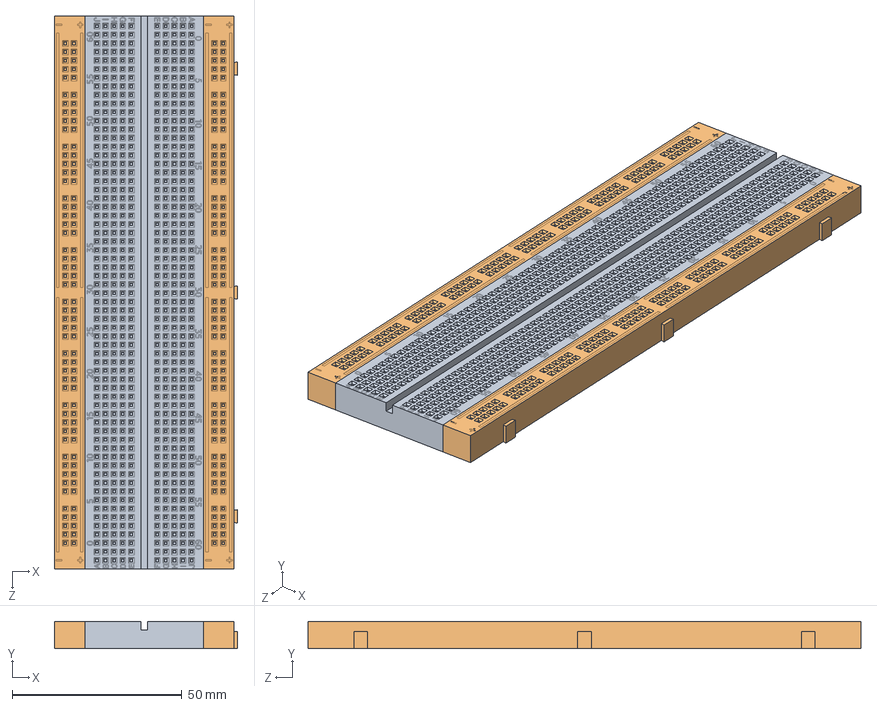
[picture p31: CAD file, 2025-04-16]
3D_модели/Основная сборка/Standard Large Breadboard with Two Side Rail.SLDASM
54.0 x 8.00 x 163.0 mm
Main Board
Side Rail x 2

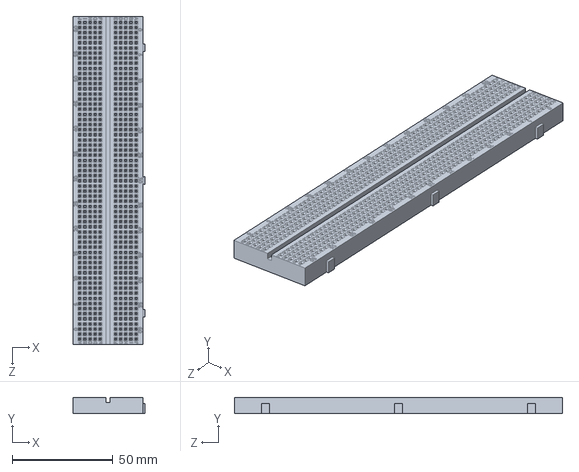
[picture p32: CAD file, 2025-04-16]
3D_модели/Основная сборка/Main Board.SLDPRT
36.0 x 8.00 x 163.0 mm

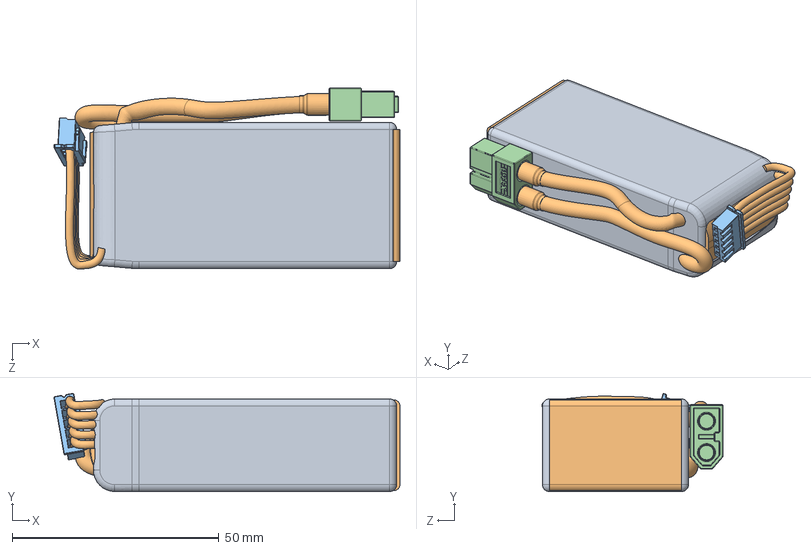
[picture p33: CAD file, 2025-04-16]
3D_модели/Испытательный стенд/TATTU 1300mah 3s.SLDASM
83.7 x 23.7 x 43.8 mm
tattu 1300MHa 3s LiPo
JST XHP-4
XT60 Buchse

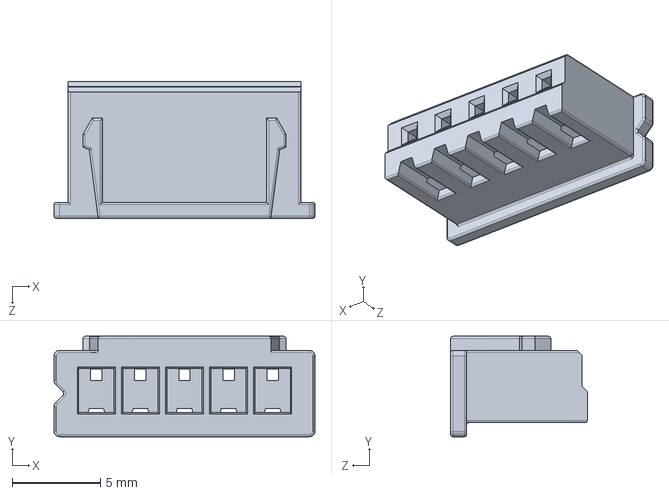
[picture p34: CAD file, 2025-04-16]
3D_модели/Испытательный стенд/JST XHP-4.sldprt
14.8 x 5.70 x 7.75 mm

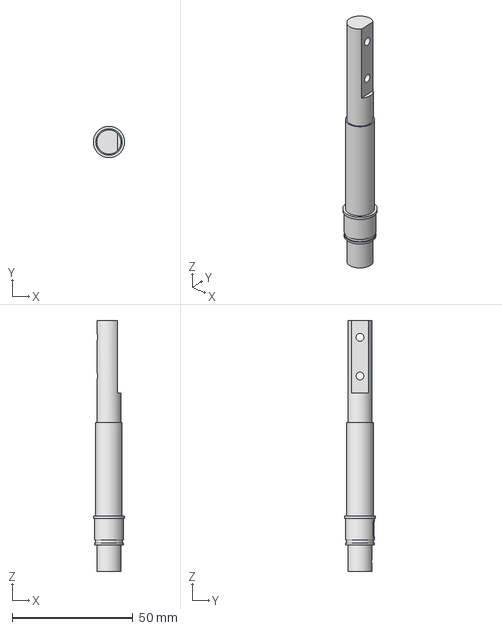
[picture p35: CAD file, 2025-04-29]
3D_модели/чертежи/Вал вертикальной оси.stp
13.0 x 13.0 x 104.0 mm

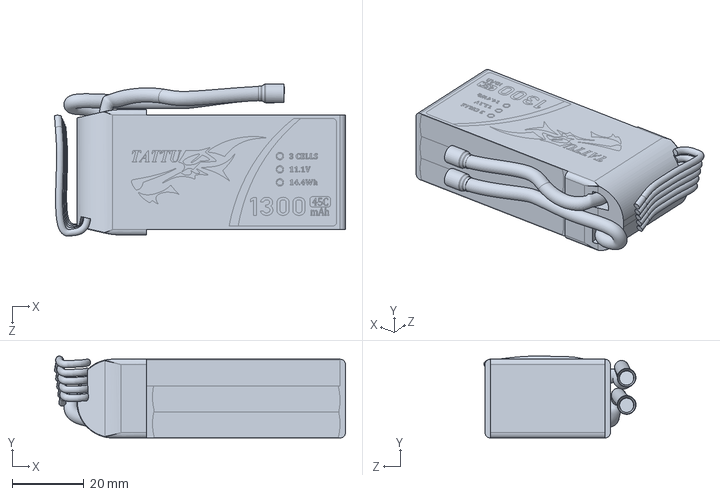
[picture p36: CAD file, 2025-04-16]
3D_модели/Испытательный стенд/tattu 1300MHa 3s LiPo.SLDPRT
81.3 x 22.9 x 42.5 mm

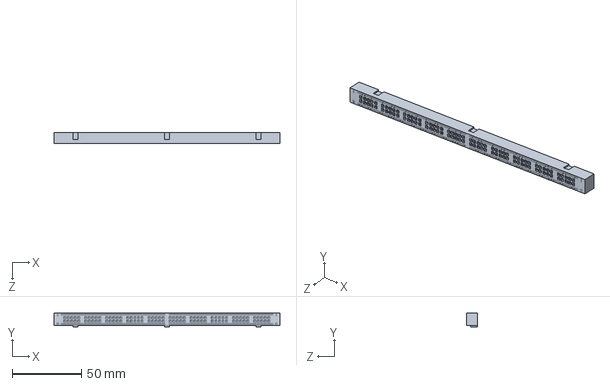
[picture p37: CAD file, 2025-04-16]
3D_модели/Основная сборка/Side Rail.SLDPRT
163.0 x 10.0 x 8.00 mm

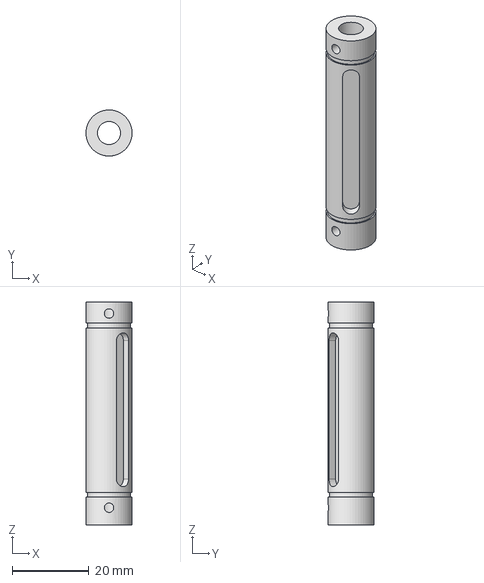
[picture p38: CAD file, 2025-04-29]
3D_модели/чертежи/Вал 2 оси.stp
12.0 x 12.0 x 58.0 mm

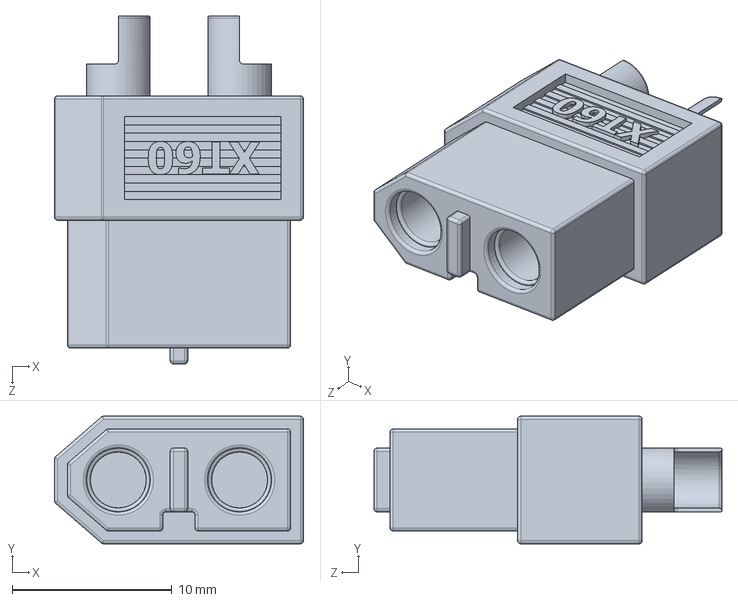
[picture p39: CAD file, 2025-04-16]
3D_модели/Испытательный стенд/XT60 Buchse.SLDPRT
15.6 x 8.00 x 21.8 mm

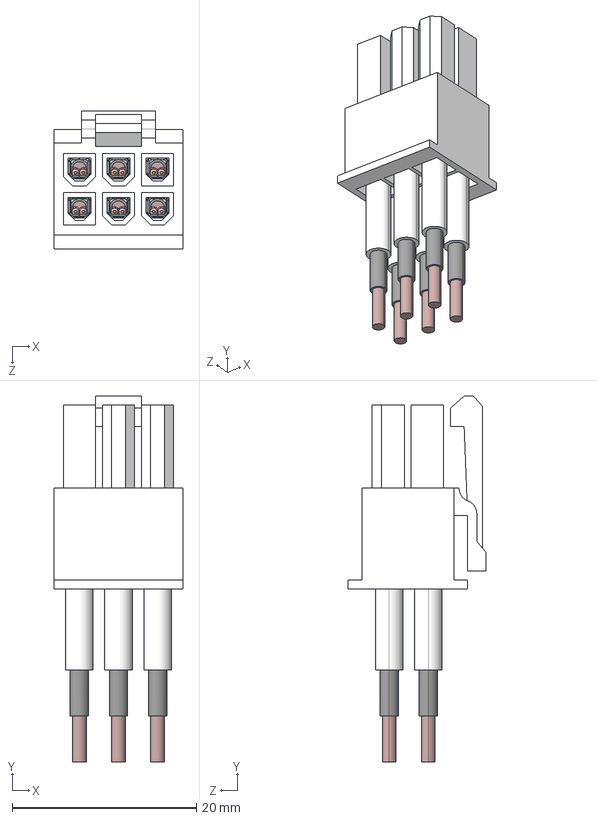
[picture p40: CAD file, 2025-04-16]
3D_модели/Основная сборка/ATX-12V-6-Pin.STEP
14.0 x 39.8 x 15.0 mm
ATX-12V-6-Pin-Body
ATX-Main-24-Pin-crimp x 6
Kabelstueck-750痠 x 6

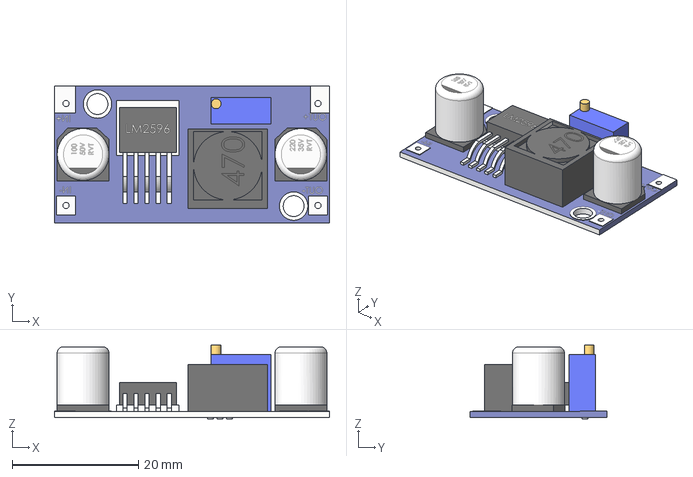
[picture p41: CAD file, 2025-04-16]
3D_модели/Испытательный стенд/LM2596 DC-DC stepdown voltage converter.step
43.5 x 21.6 x 11.7 mm

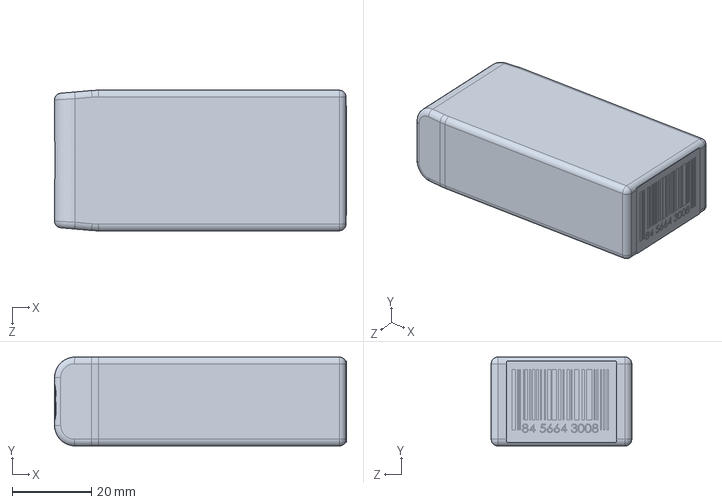
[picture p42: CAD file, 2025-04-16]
3D_модели/Испытательный стенд/FUNDA 13.SLDPRT
73.5 x 22.4 x 35.4 mm

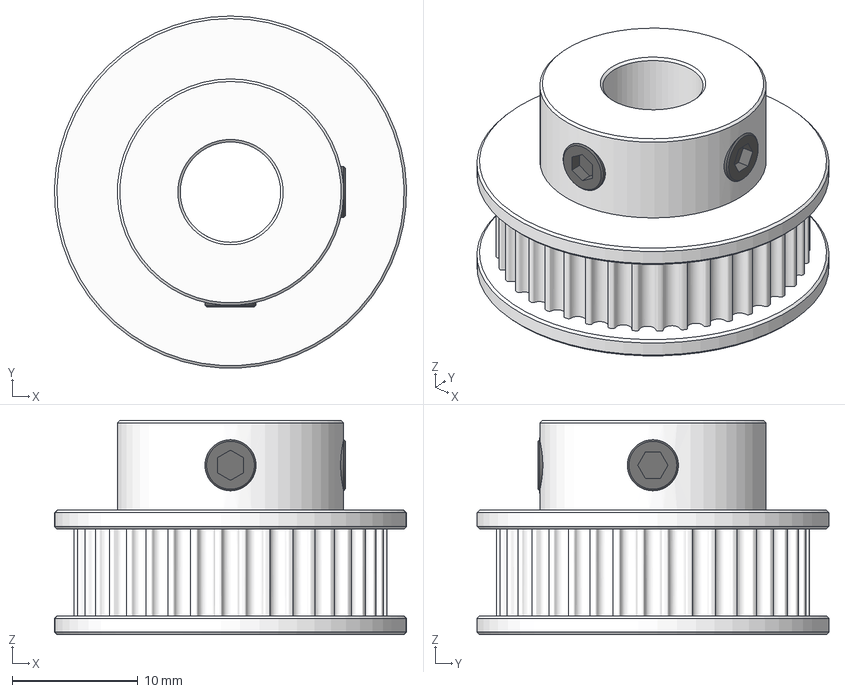
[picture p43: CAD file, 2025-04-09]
3D_модели/Основная сборка/GT2 40T 8 Bore v2.step
28.0 x 28.0 x 17.1 mm
Pulley
Screw v1
Screw v1 (1)

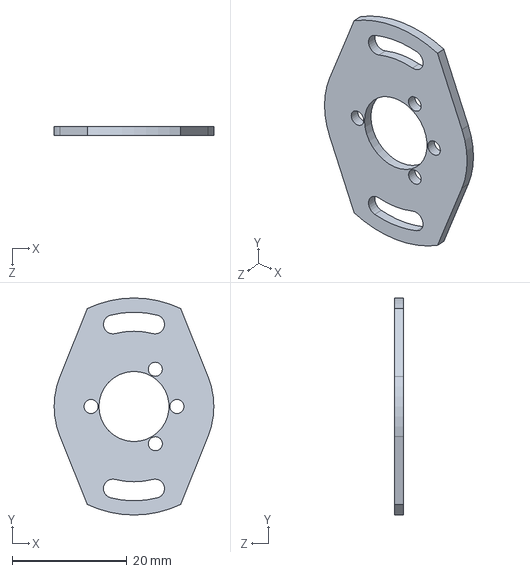
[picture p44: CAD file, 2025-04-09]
3D_модели/Основная сборка/Holder Adjustable P3022-V1-CW360.SLDPRT
27.8 x 37.8 x 1.60 mm

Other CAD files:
Dual_BLDC_Controller/PCB_board.DWG
3D_модели/Испытательный стенд/rotary+encoder_17mm_hole_spc.stp
3D_модели/OldVersions/Провода.0001.ipt
3D_модели/Вспомогательные модели/OldVersions/Грубый_макет.0001.ipt
3D_модели/Вспомогательные модели/OldVersions/Двигатель.0001.ipt
3D_модели/Вспомогательные модели/OldVersions/Макет_рамки.0001.ipt
3D_модели/Вспомогательные модели/OldVersions/Ось_антенны.0001.ipt
3D_модели/Вспомогательные модели/Антенна.ipt
3D_модели/Вспомогательные модели/Грубая сборка.iam
3D_модели/Вспомогательные модели/Двигатель.ipt
3D_модели/Вспомогательные модели/Макет_рамки.ipt
3D_модели/Вспомогательные модели/Ось_антенны.ipt
3D_модели/Вспомогательные модели/Редуктор.ipt
3D_модели/Вспомогательные модели/Энкодер.ipt
3D_модели/Испытательный стенд/FUNDA 13.ipt
3D_модели/Испытательный стенд/JST XHP-4.ipt
3D_модели/Испытательный стенд/LM2596 DC-DC stepdown voltage converter.ipt
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

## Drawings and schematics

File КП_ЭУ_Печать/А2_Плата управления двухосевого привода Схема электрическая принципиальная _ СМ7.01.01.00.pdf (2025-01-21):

### M32G474 D1

# Схема блока СМ7.01.01.01 Phase_A Phase_B Phase_C Hall_A Hall_B Hall_C Speed_FB

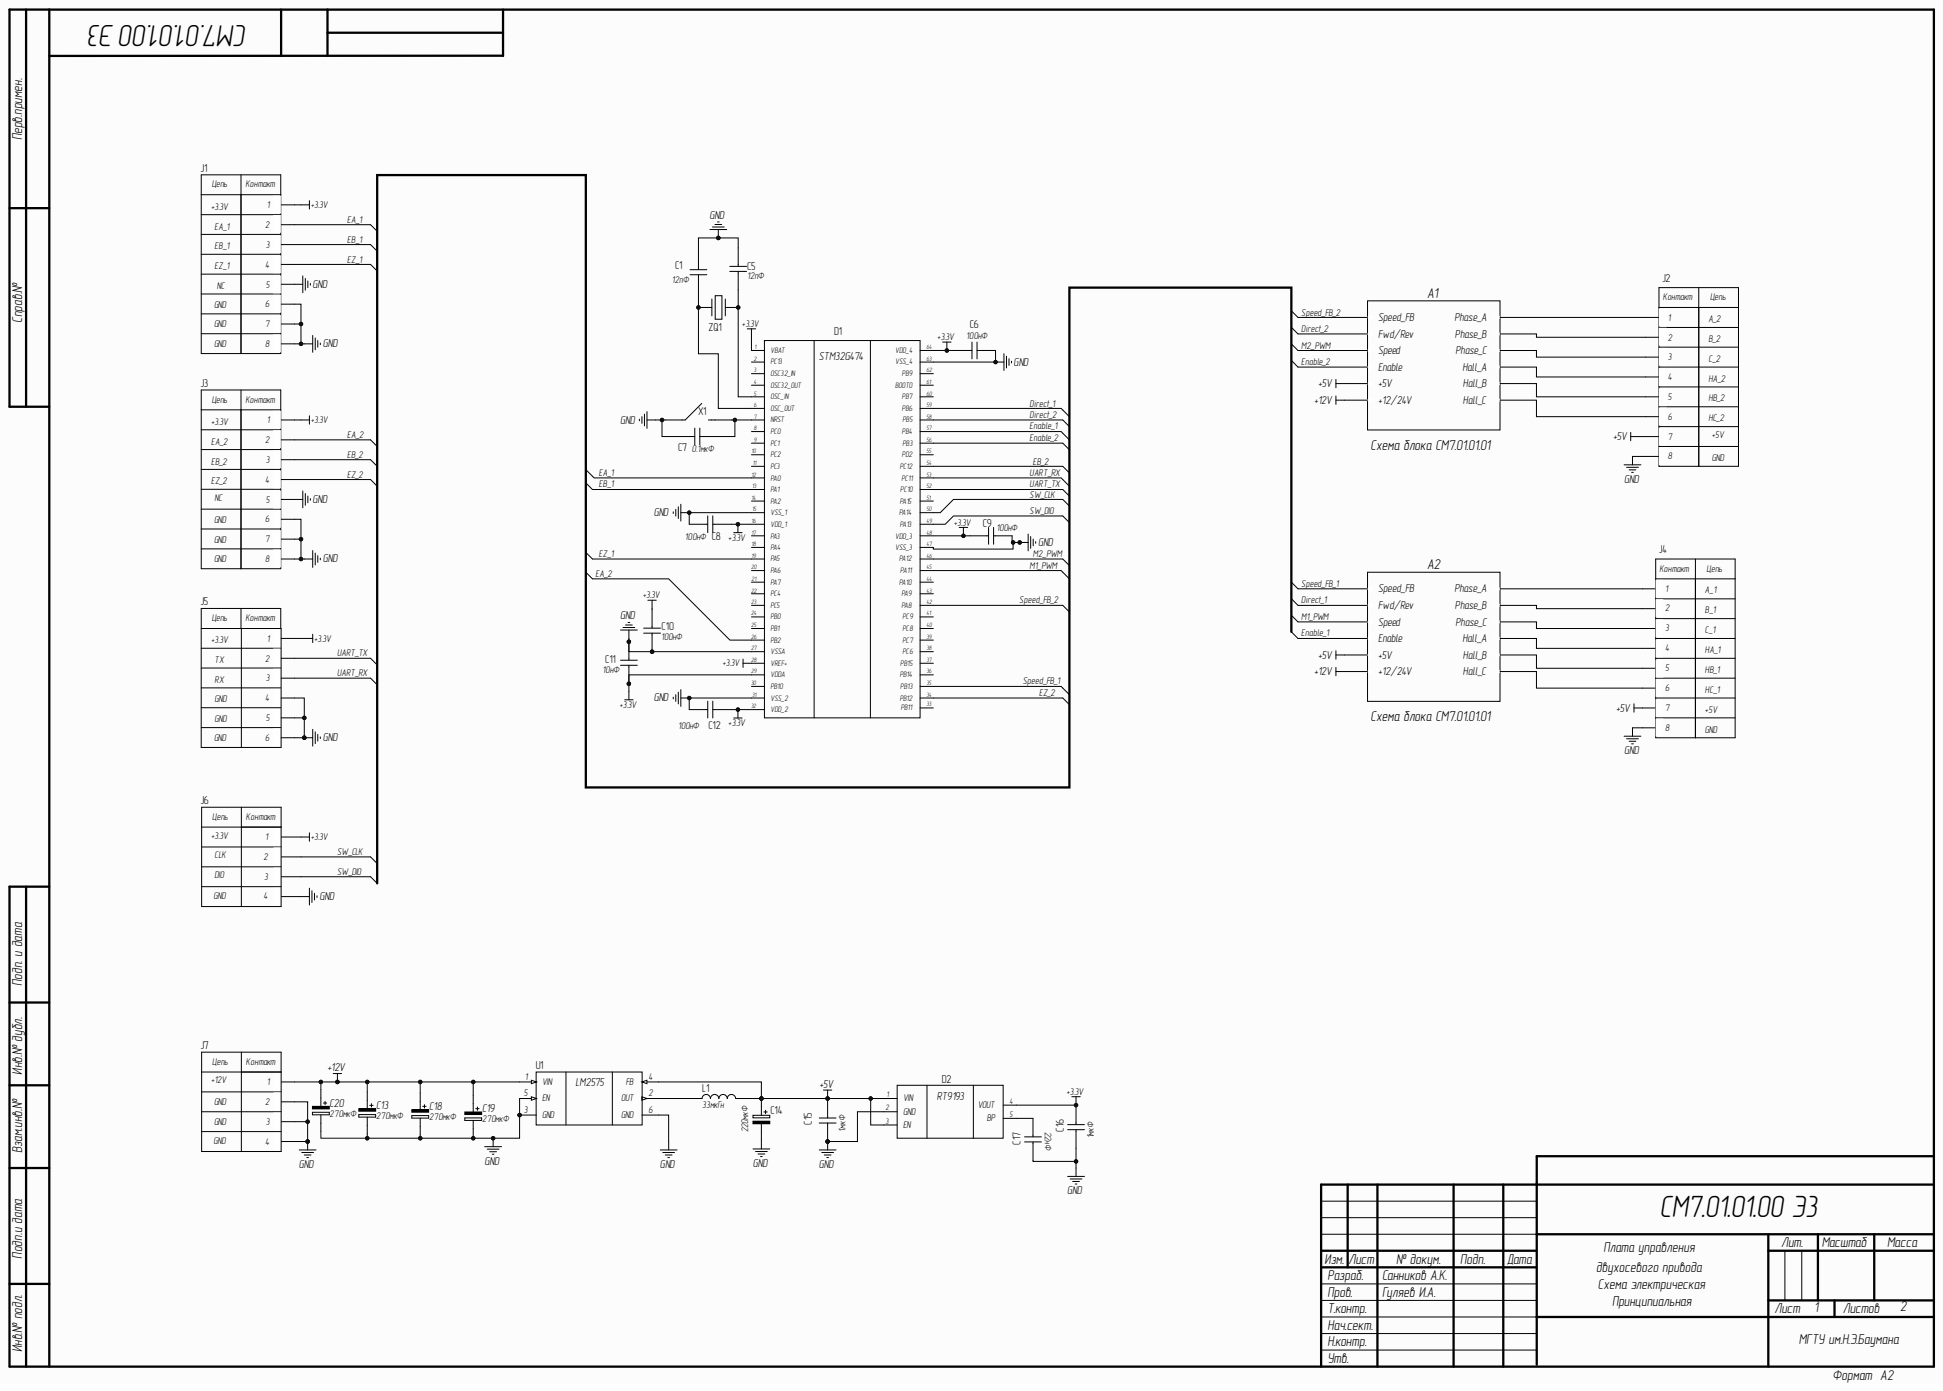
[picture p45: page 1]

Це пь | К о нтакт

+ 3.3V
3.3VNC NC EA_1 EB_1 EZ_1 EA_2 EB_2 EZ_2 GND GND GND

К о нтакт | Це пь

R X | 123456

3.3VDIO CLK | 1234

Инв.№ подл. Подп.и дата Взам.инв.№ Инв.№ дубл. Подп. и дата

Плата управления двухосевого привода Схема электрическая Принципиальная | Лит. | Масш таб | Масса
Изм. | Лист | № докум. | Подп. | Дат а
Разраб. | | Санников А. К.
Пров. | | Гуляев И. А.
Т. контр . | | | | | Лист | Листов 2
Нач.сект. | | | | | Н. Э.Баумана
Н. контр .
Утв.

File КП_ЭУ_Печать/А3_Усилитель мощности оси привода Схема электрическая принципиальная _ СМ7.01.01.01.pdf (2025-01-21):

# Enable +5V

# B1 VCC

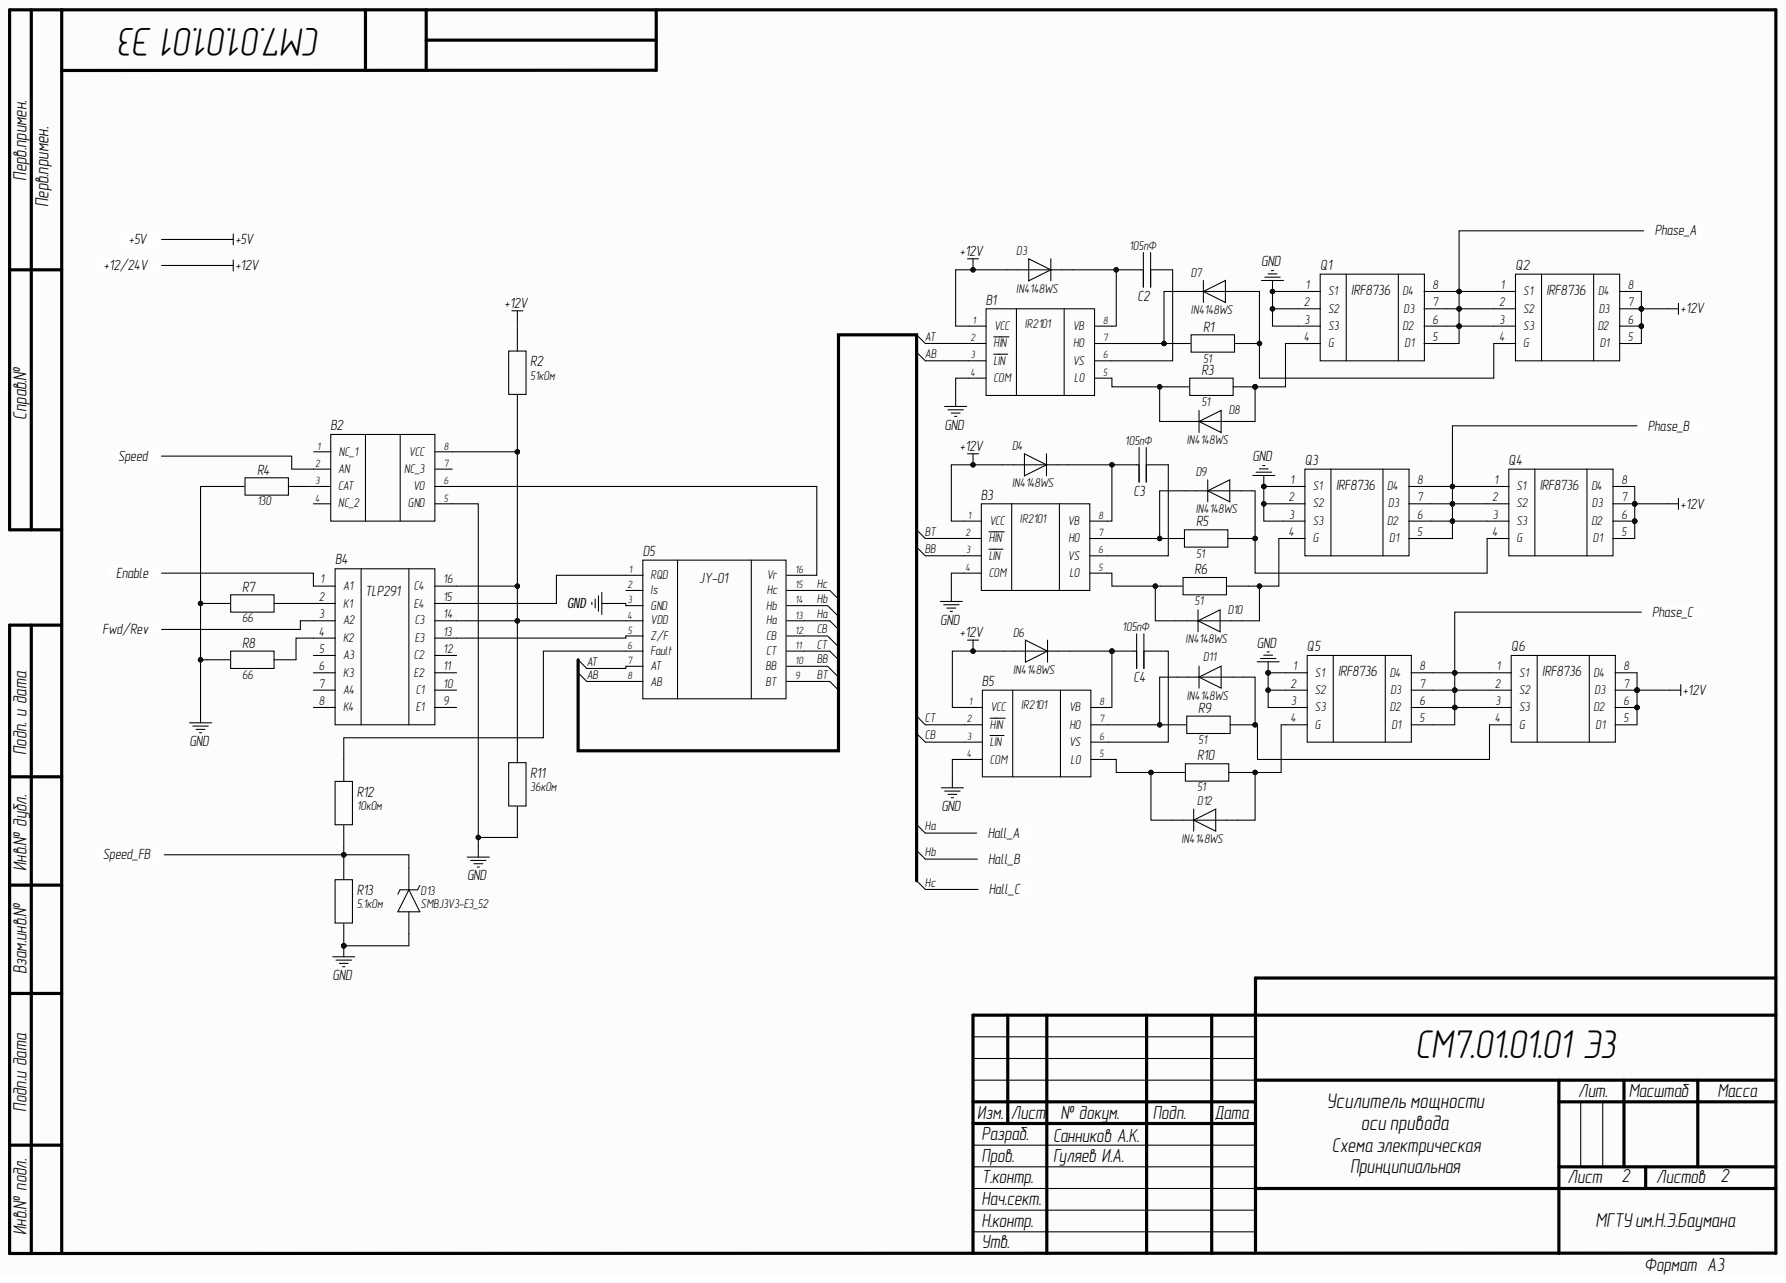
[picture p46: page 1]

Инв.№ подл. Подп.и дата Взам.инв.№ Инв.№ дубл. Подп. и дата

Изм. | № докум. | Подп. | Дата | | Лист Лит. | | Масштаб

Ус и л и т е л ь м о щ н о с т и о с и пр и во да Схема электрическая Принципиаль ная | | Масса
контр. Лист Разраб. | Санников А. К.
Пров. | Гуляев И. А.
Т. | | | | 2 | 2 Листов
Нач.сект. | | | | МГТУ им . Н. Э.Баумана
Н. контр.
Утв.

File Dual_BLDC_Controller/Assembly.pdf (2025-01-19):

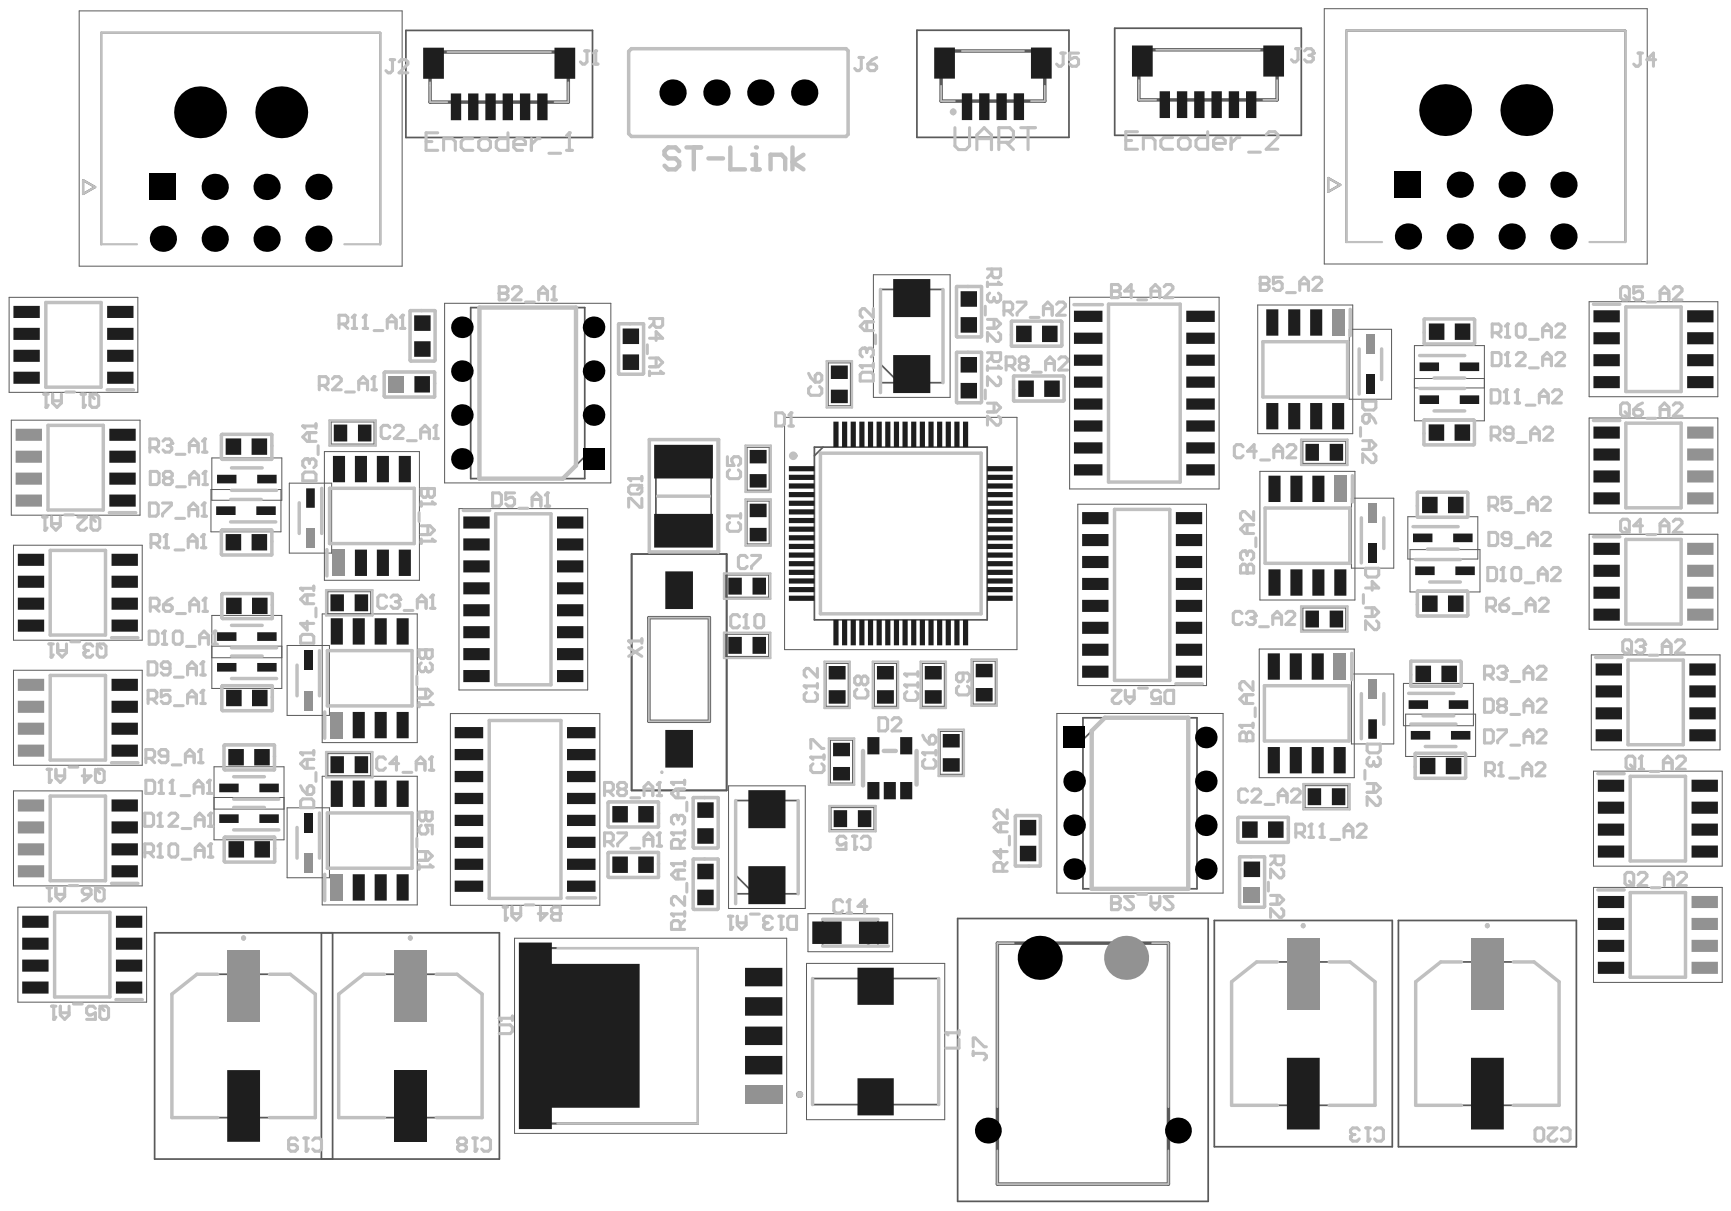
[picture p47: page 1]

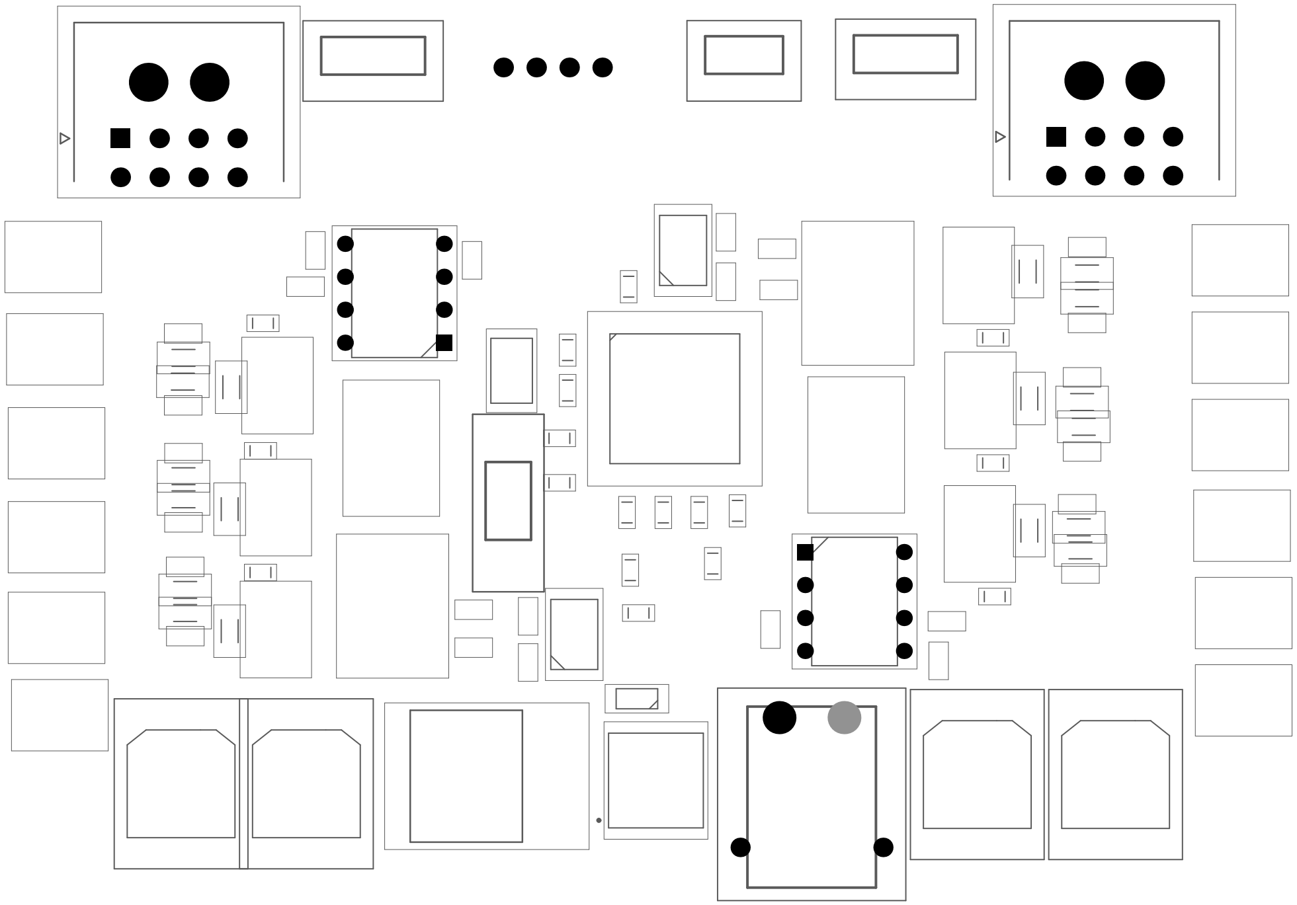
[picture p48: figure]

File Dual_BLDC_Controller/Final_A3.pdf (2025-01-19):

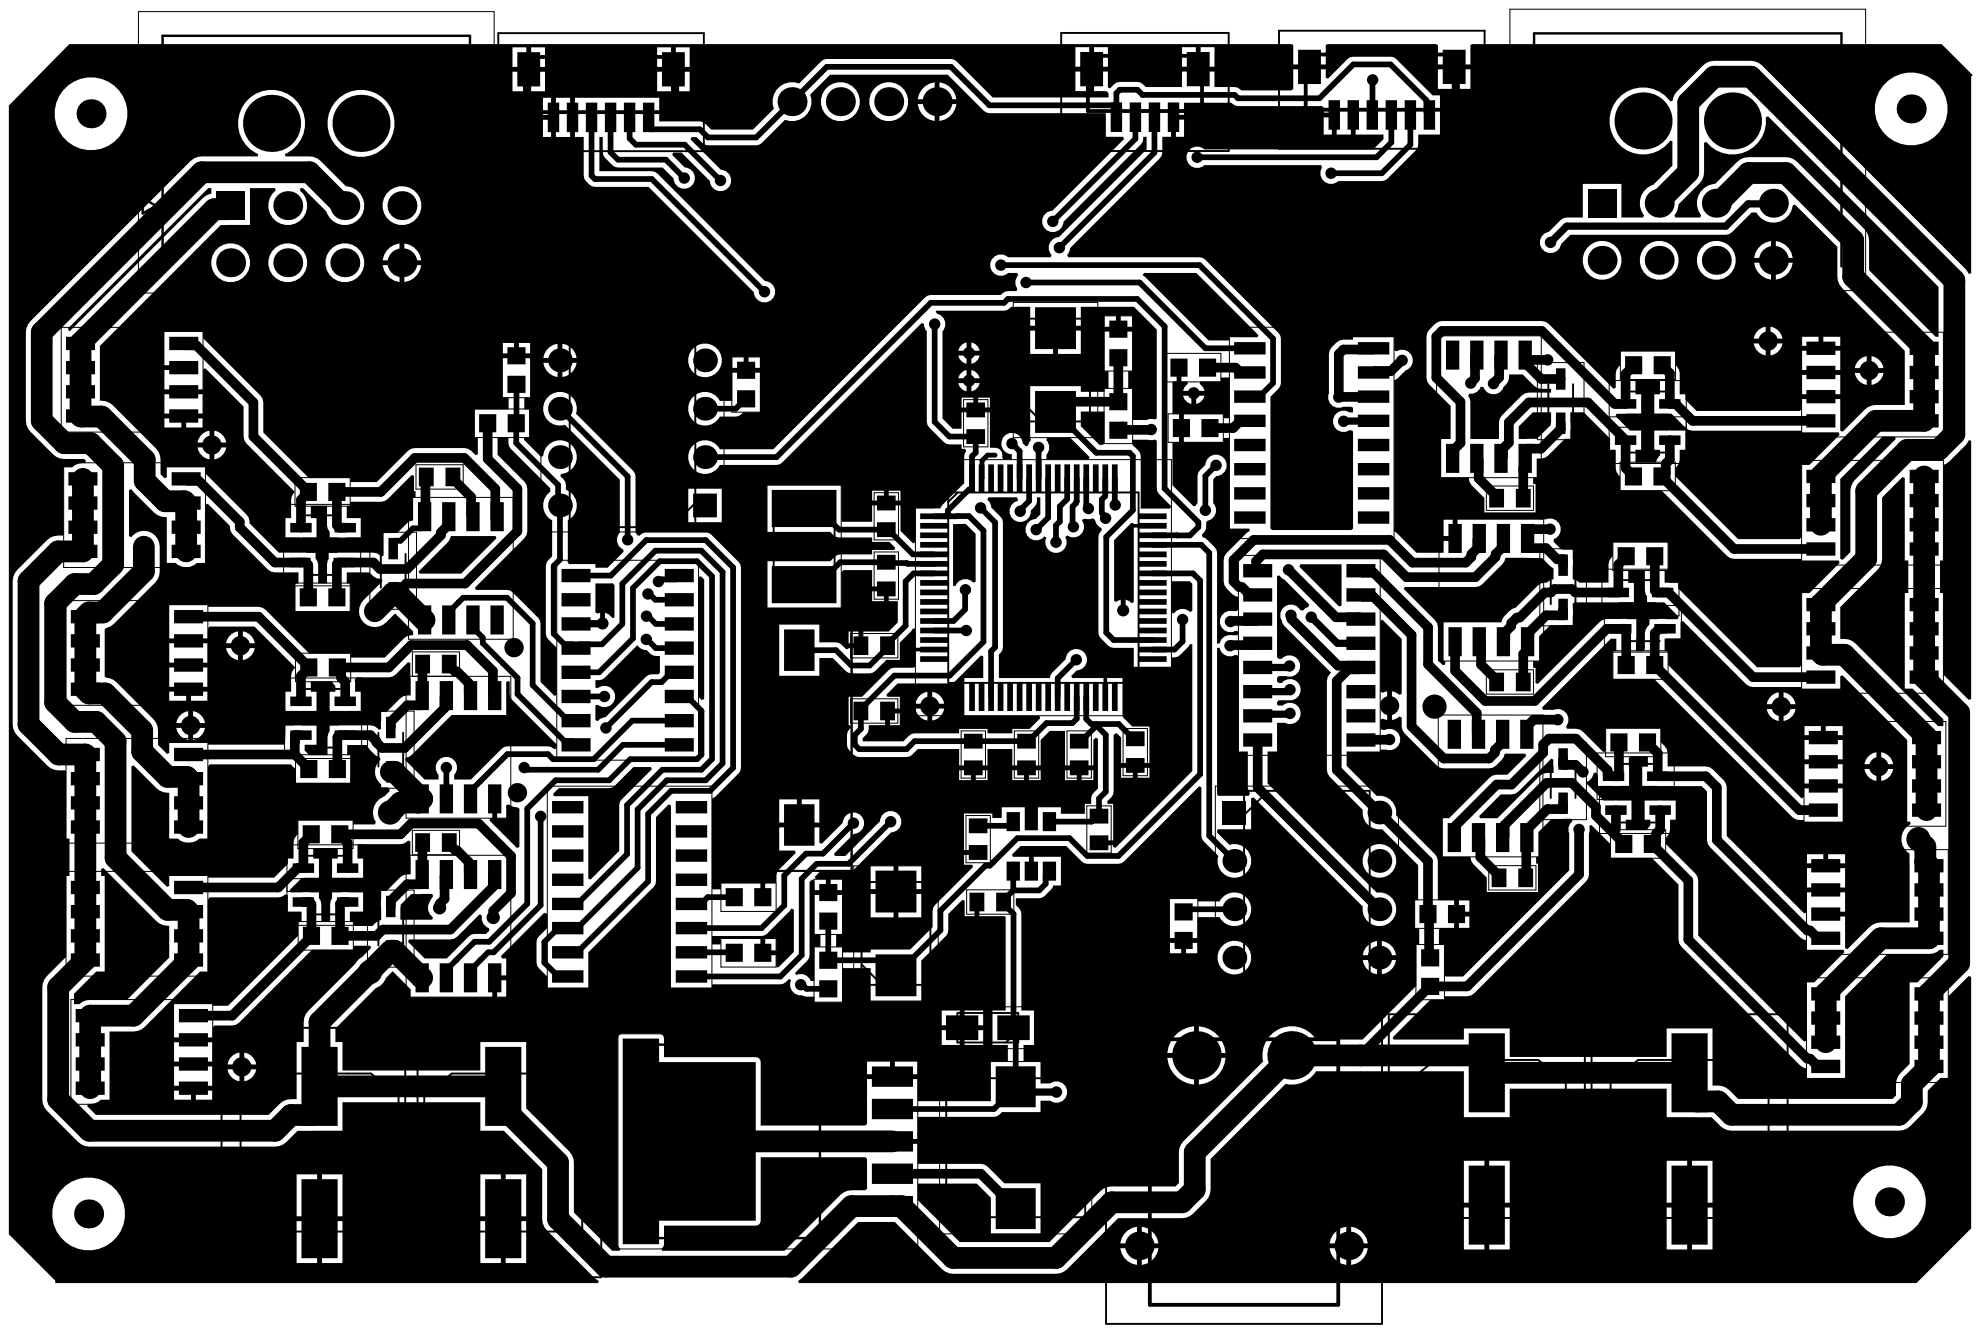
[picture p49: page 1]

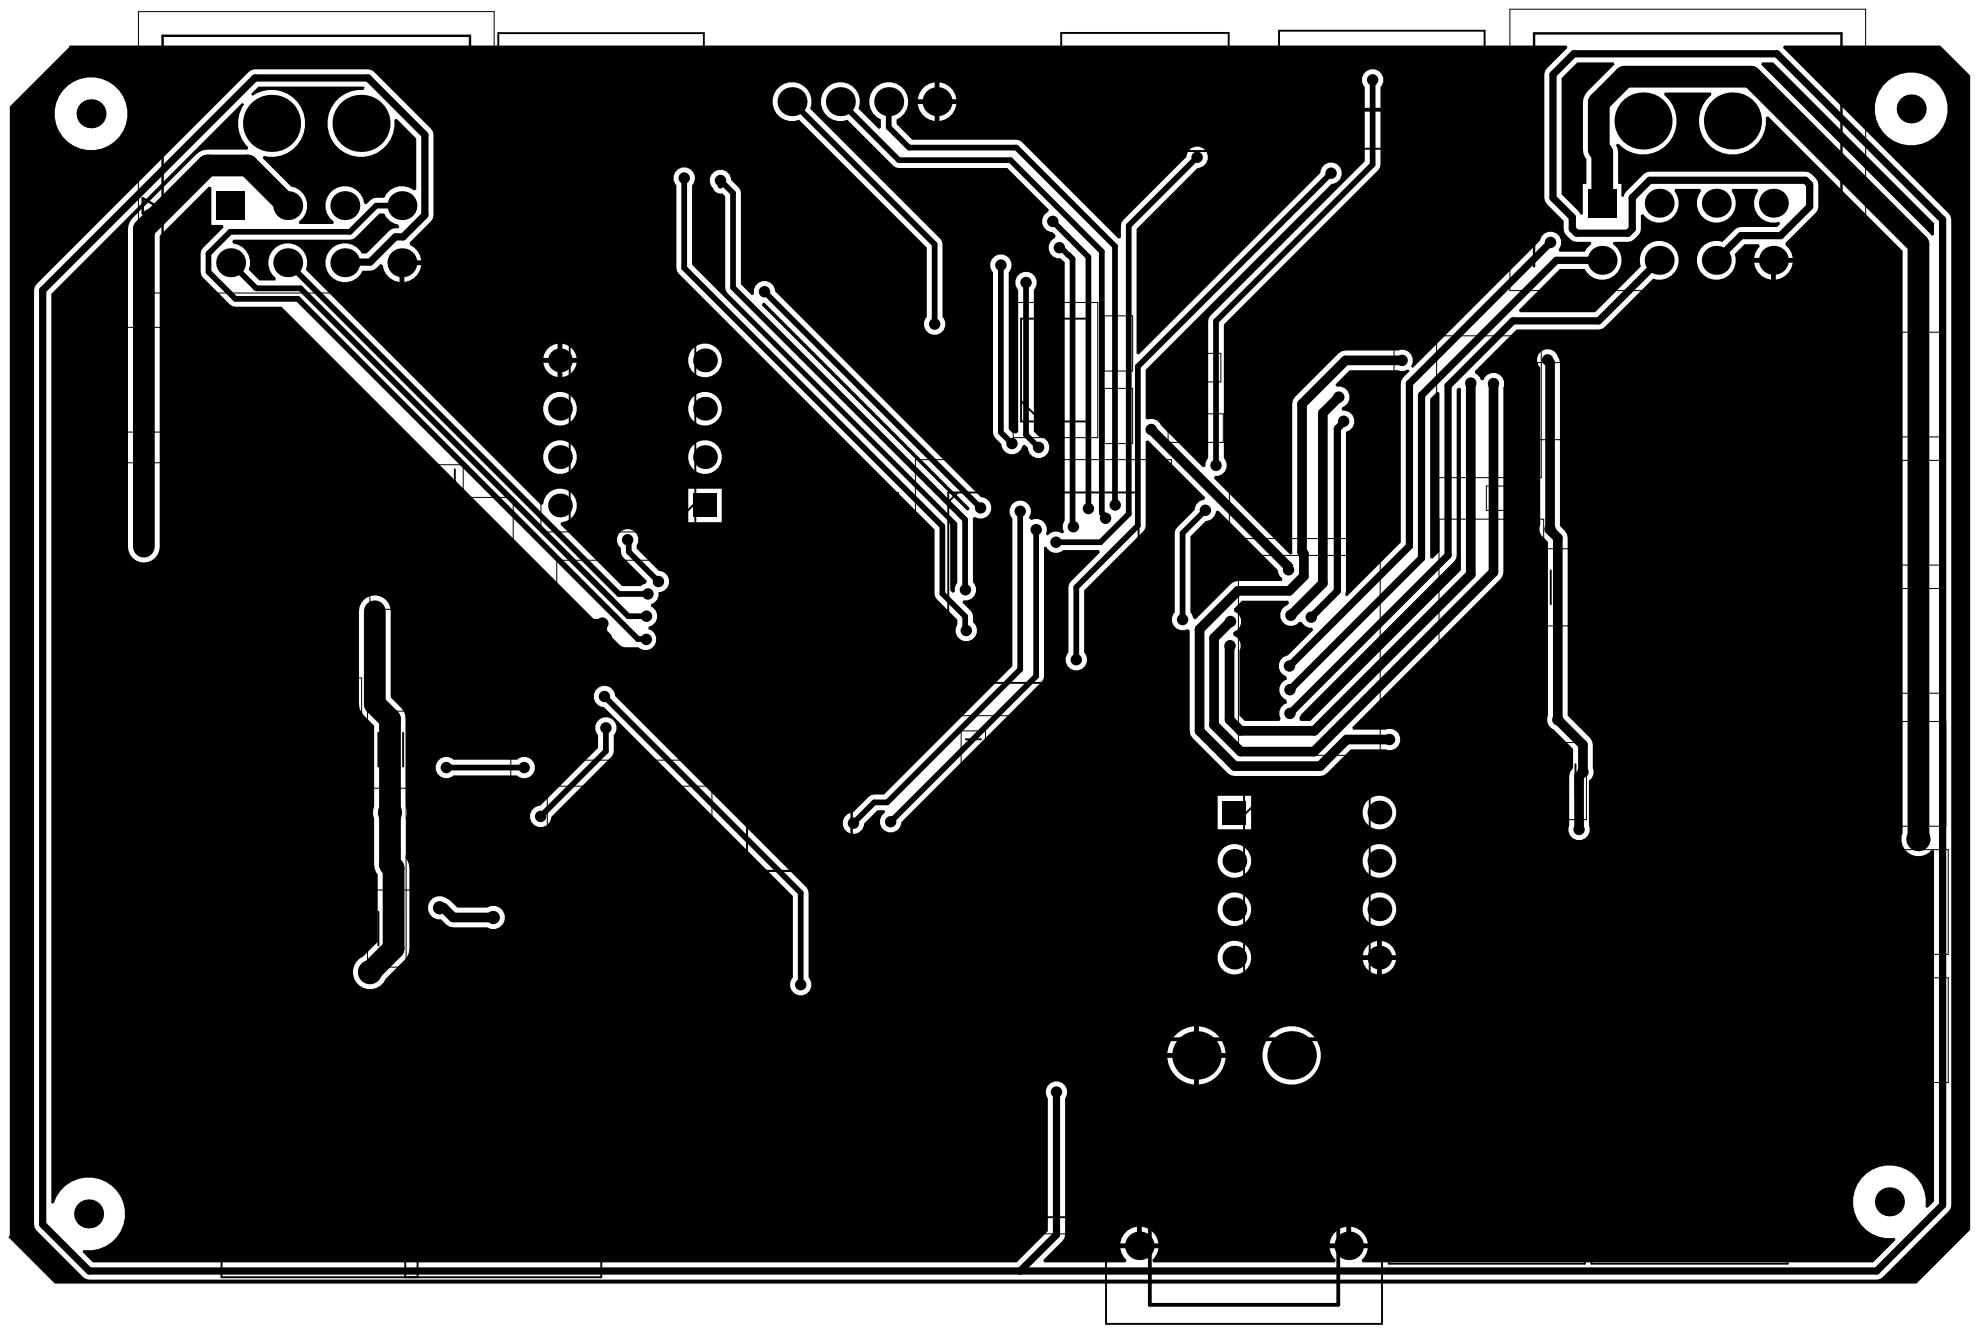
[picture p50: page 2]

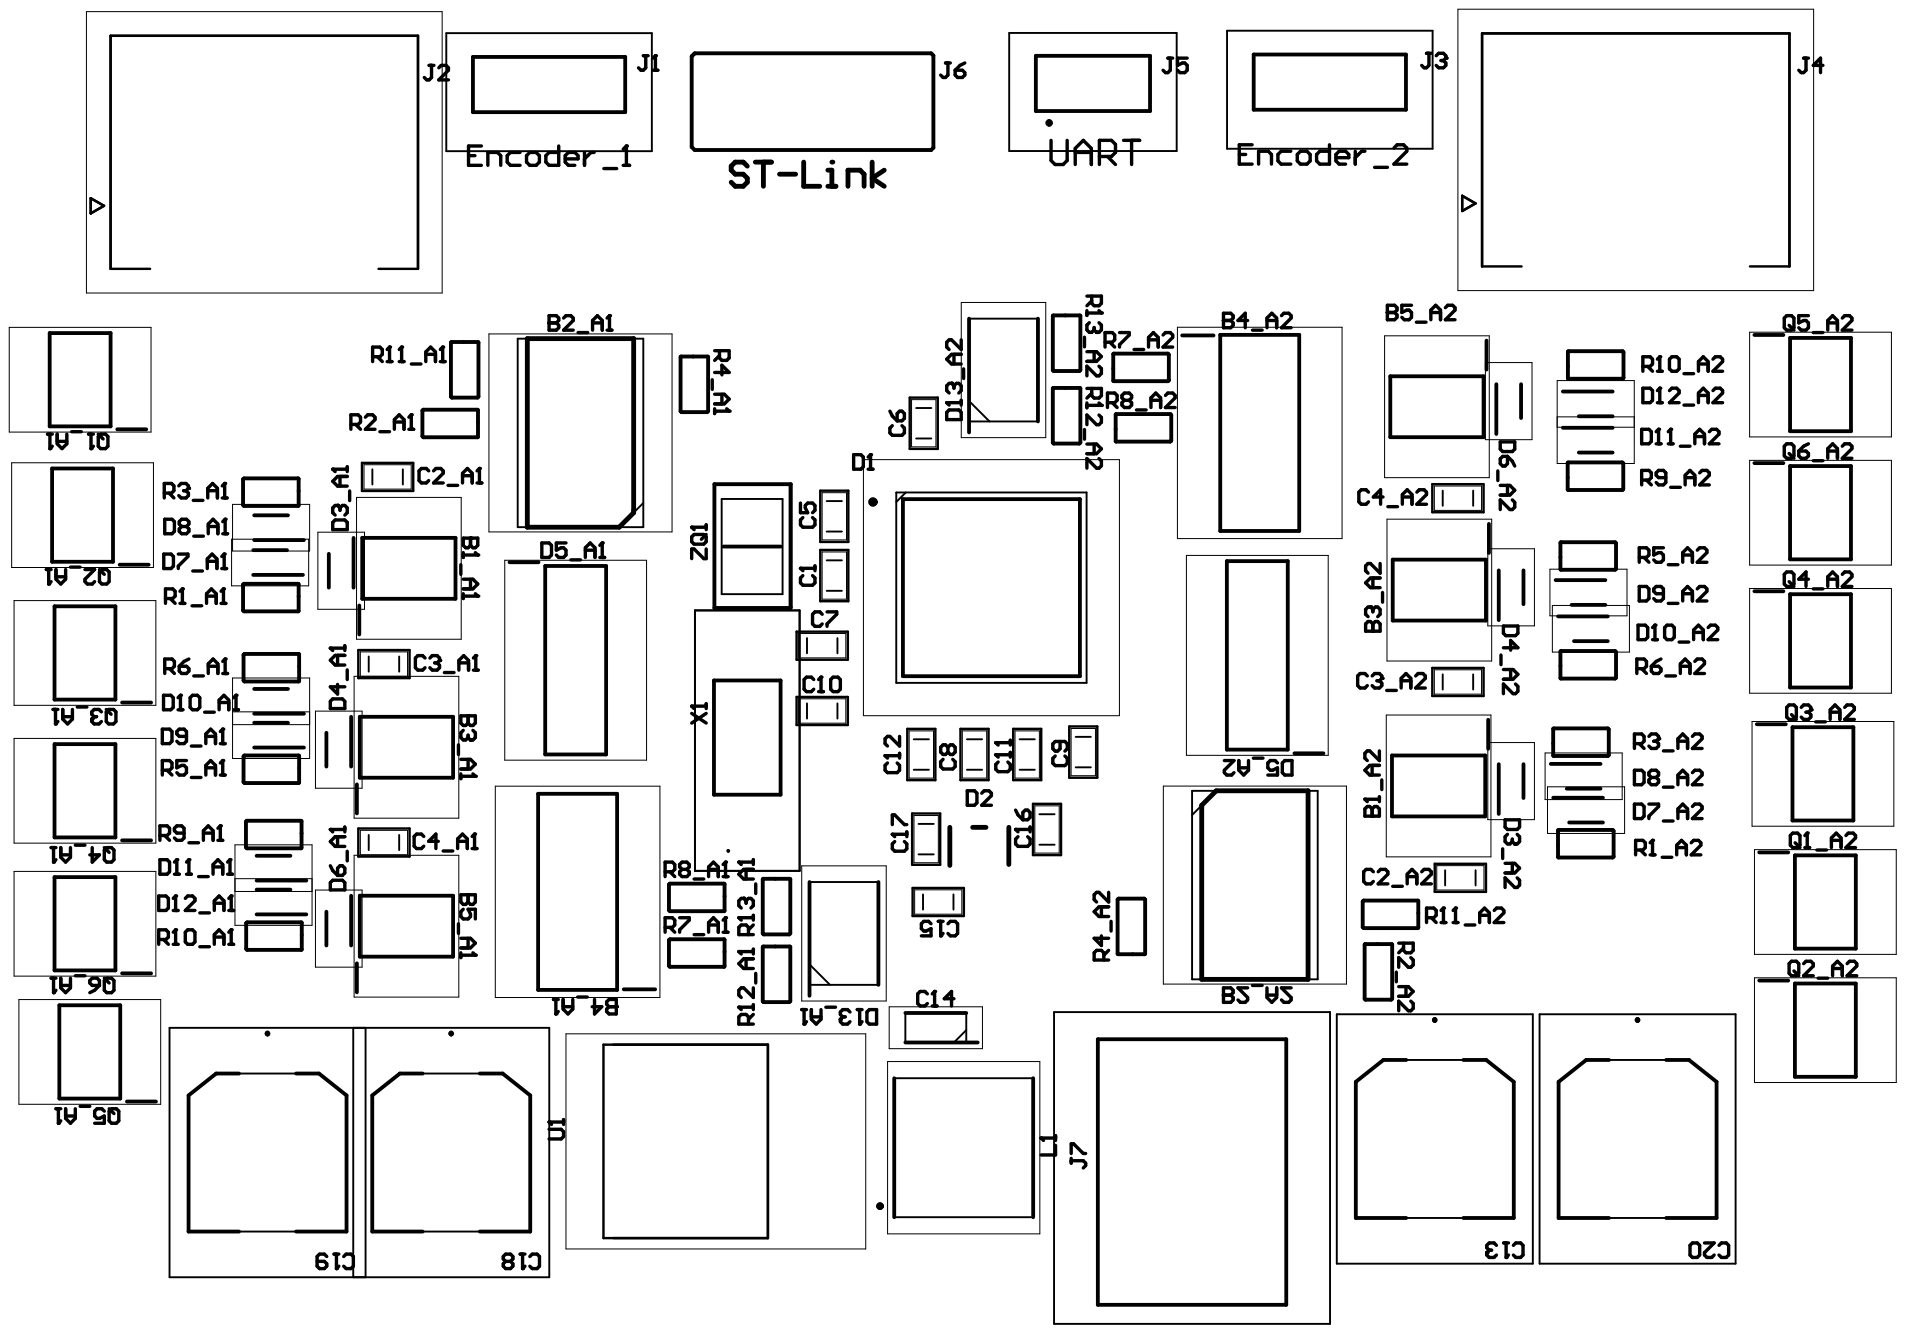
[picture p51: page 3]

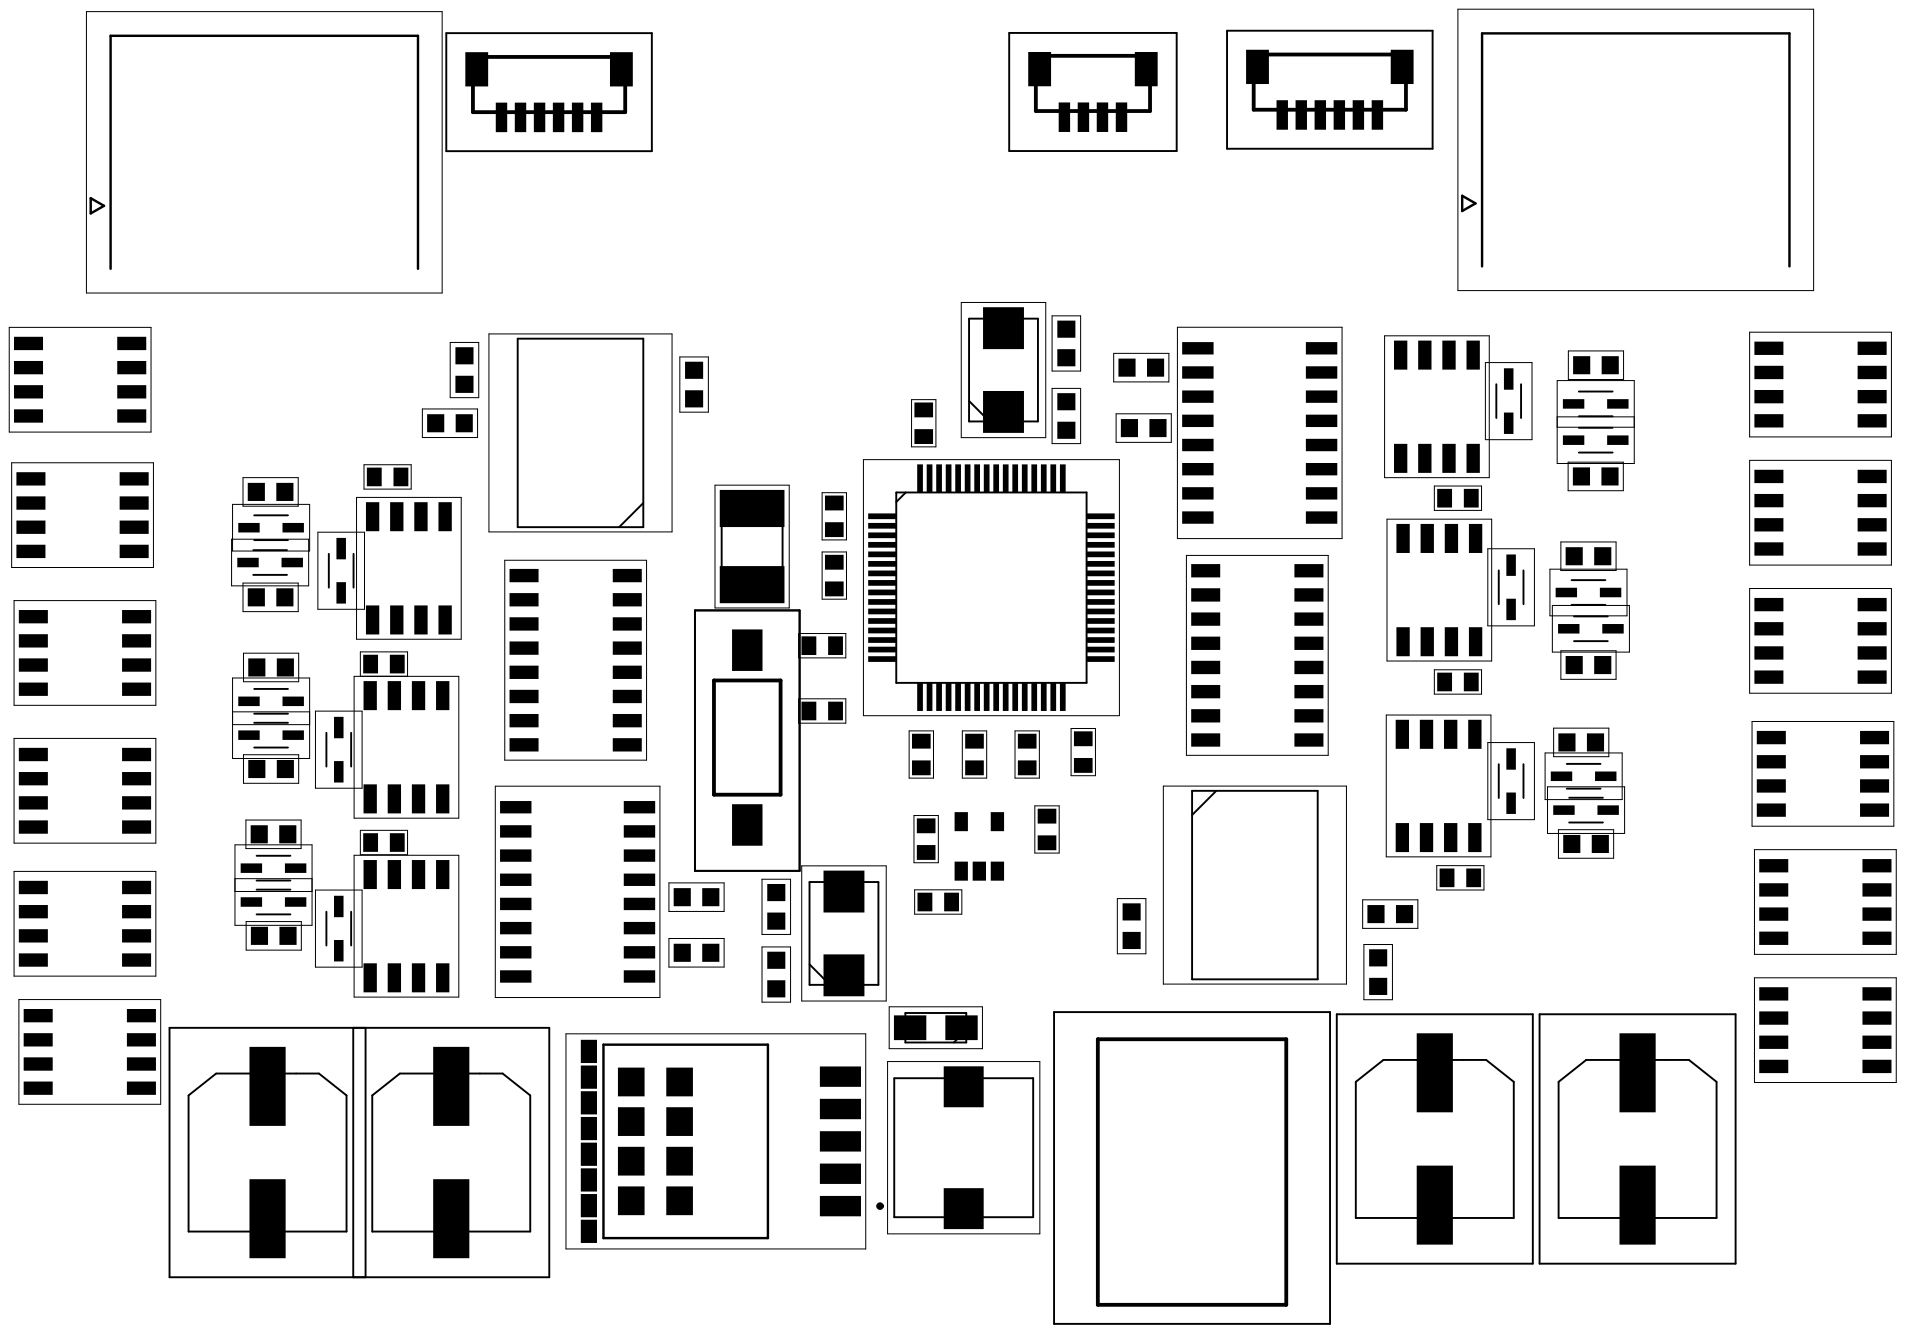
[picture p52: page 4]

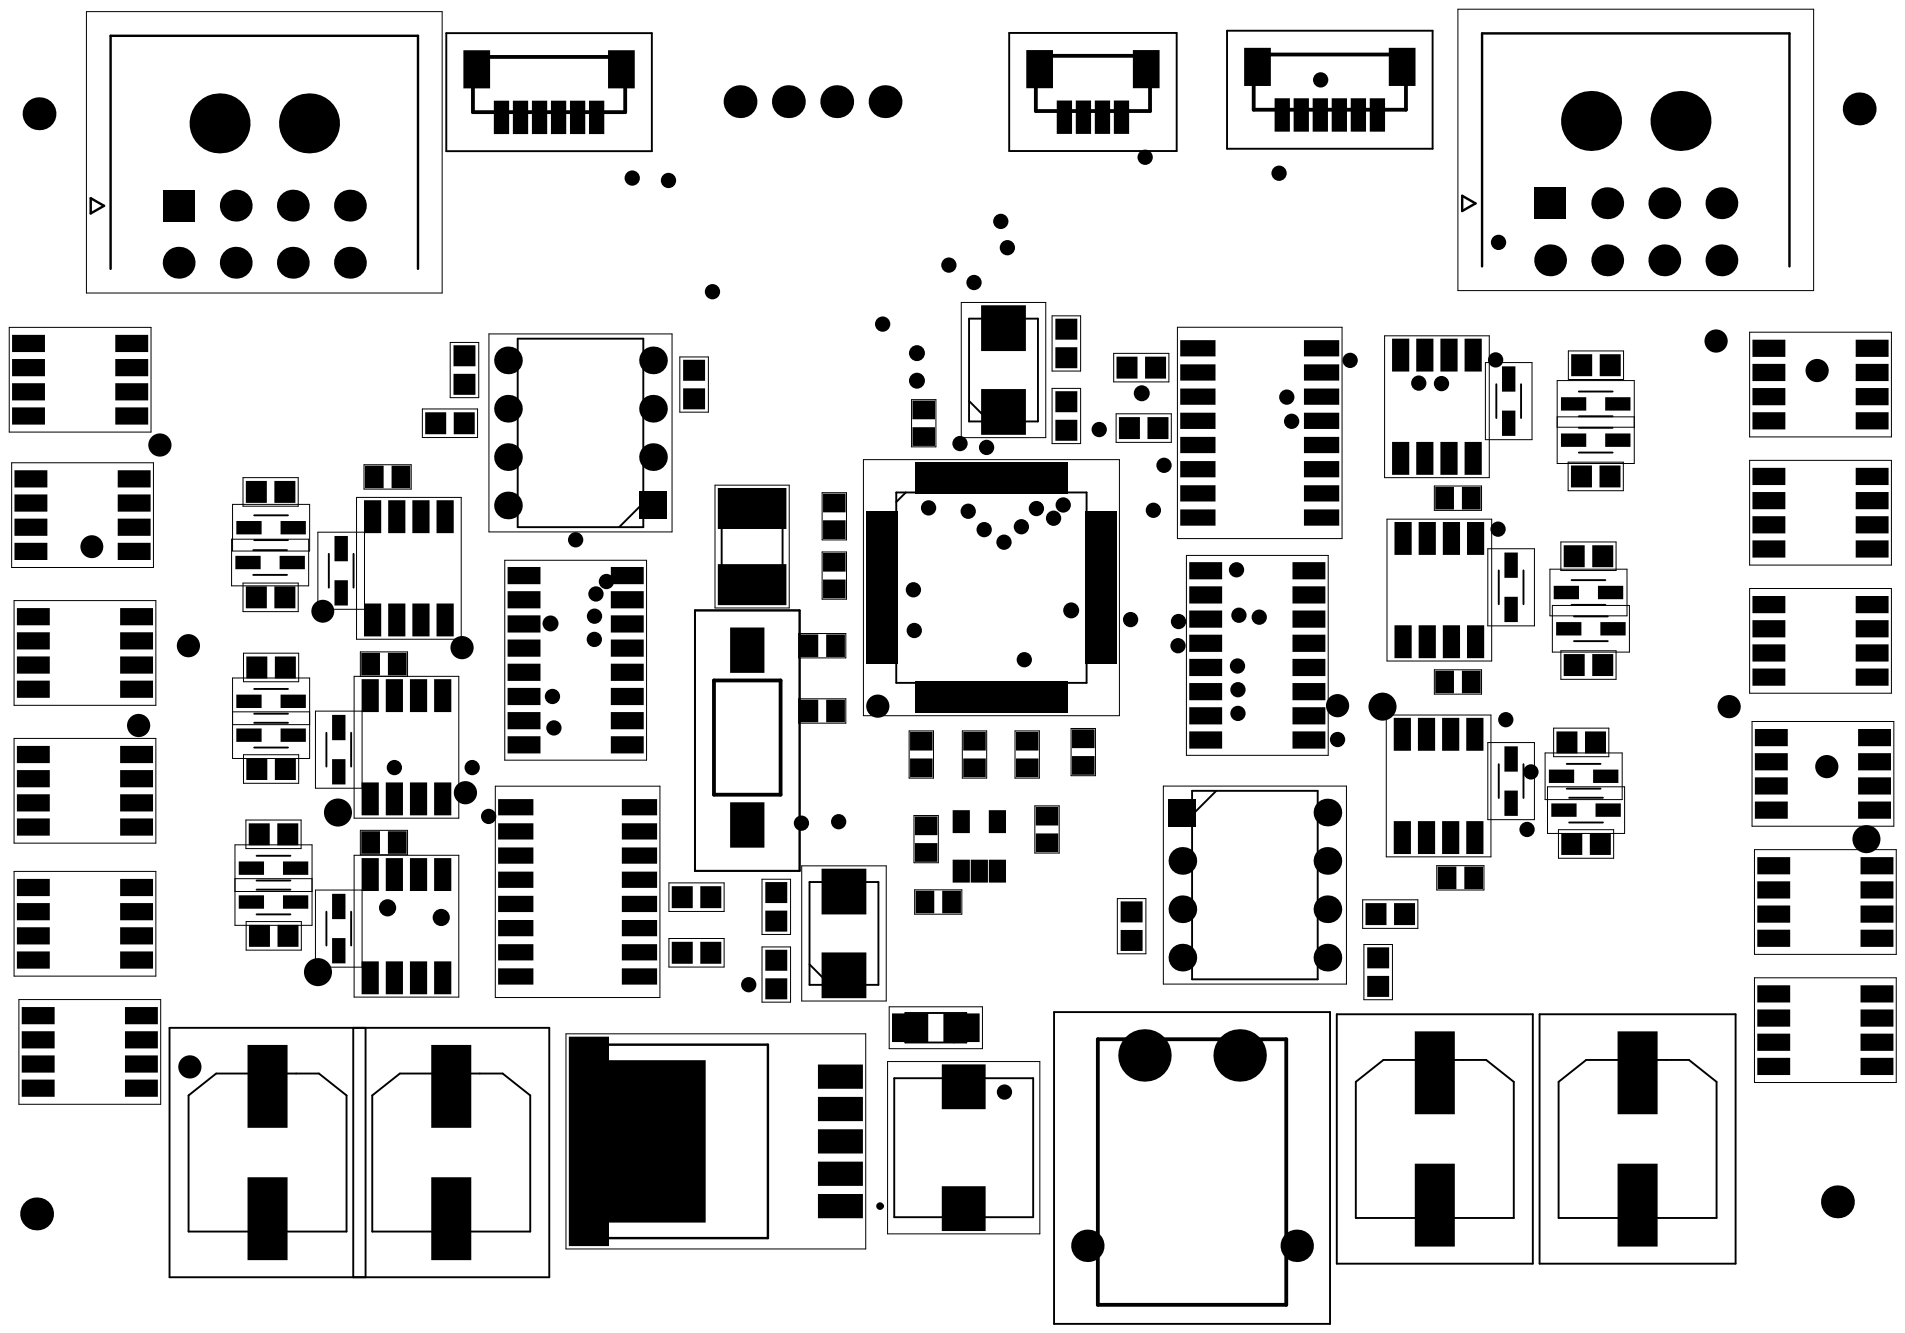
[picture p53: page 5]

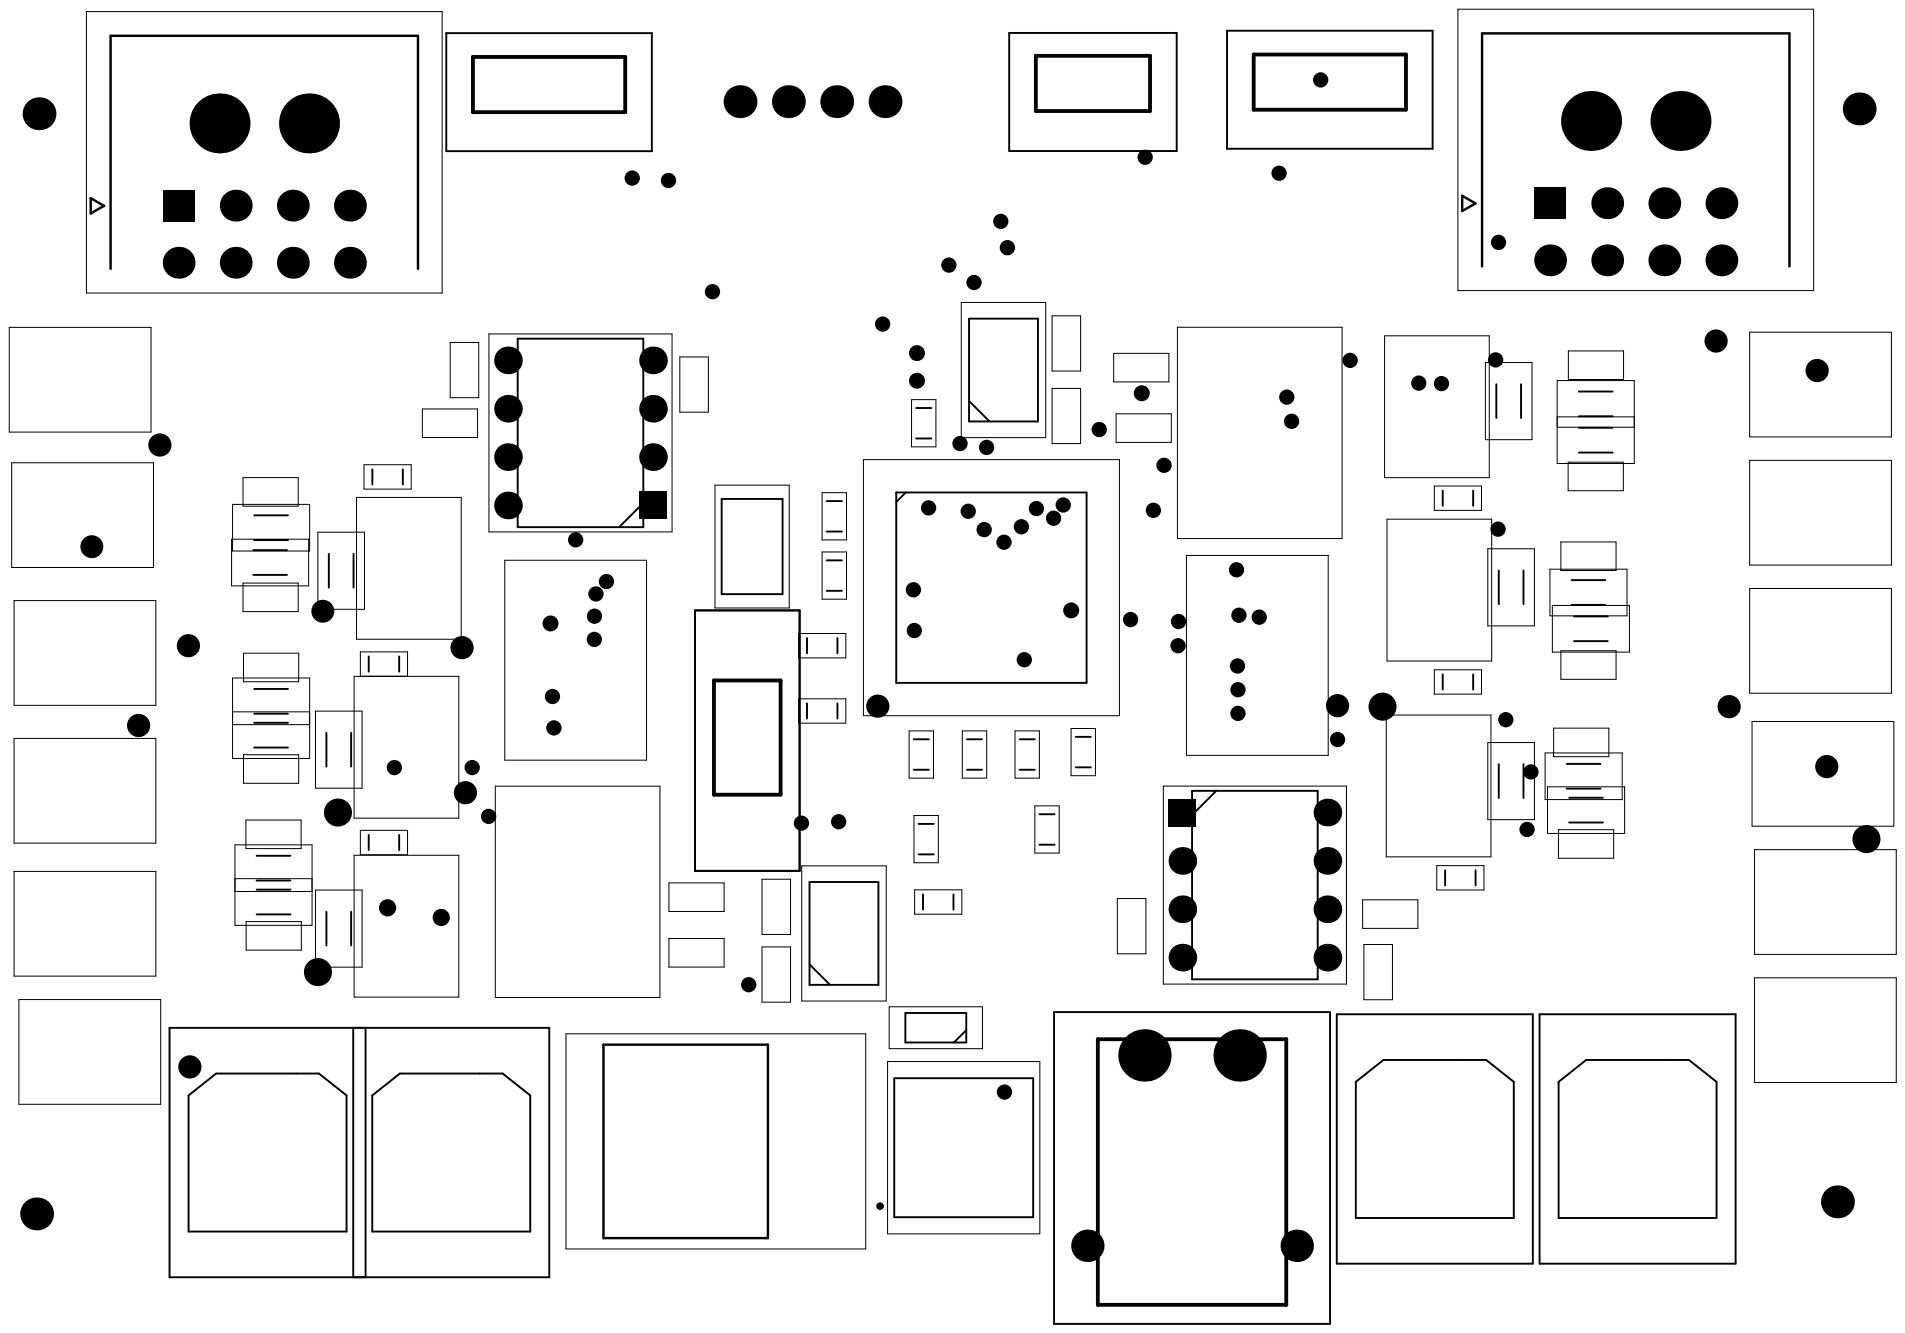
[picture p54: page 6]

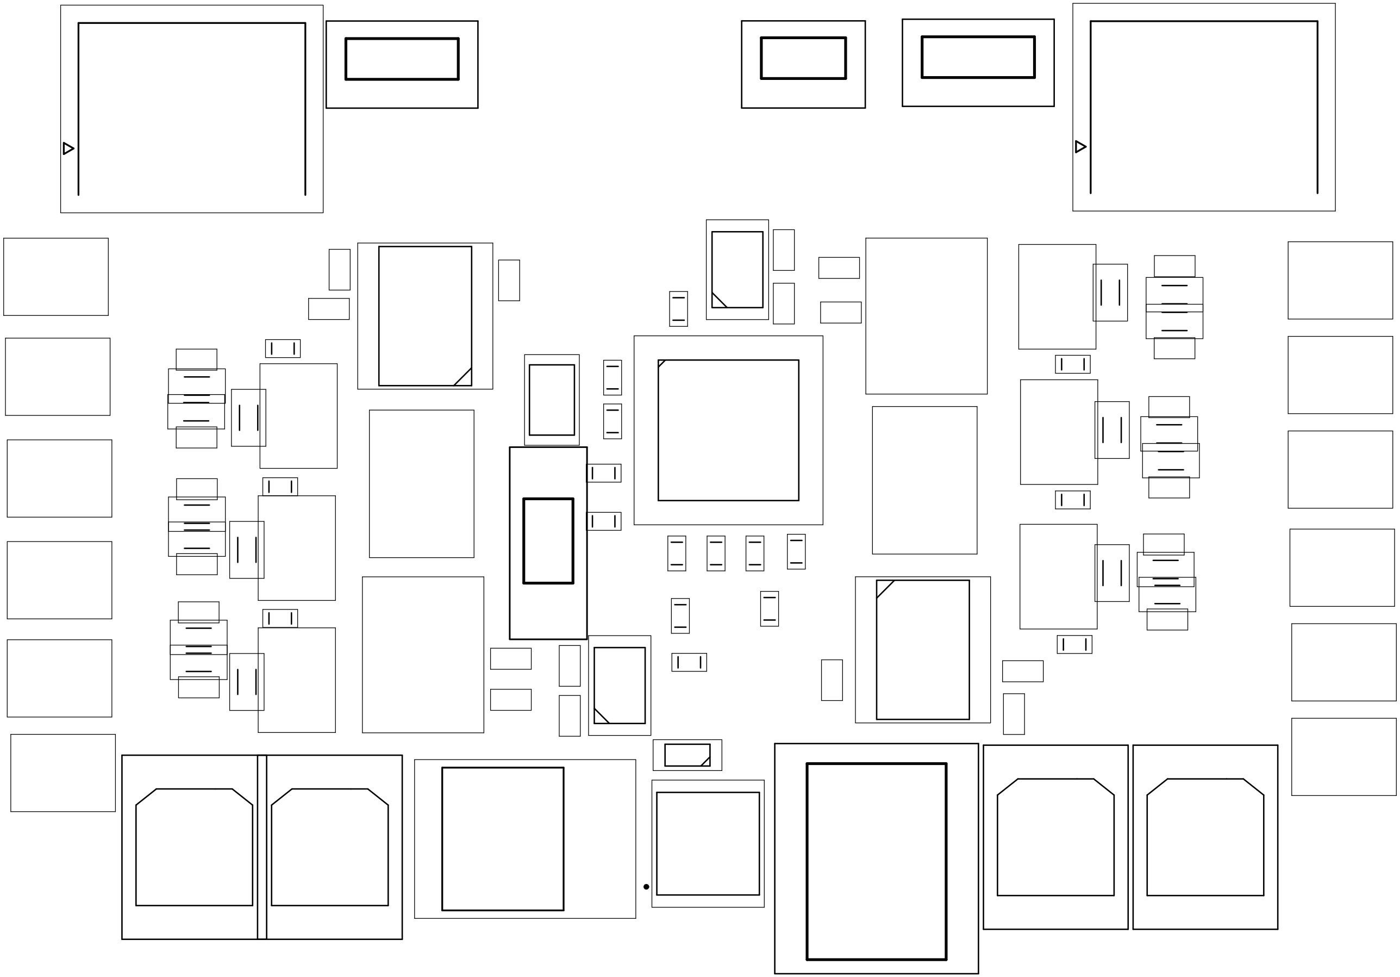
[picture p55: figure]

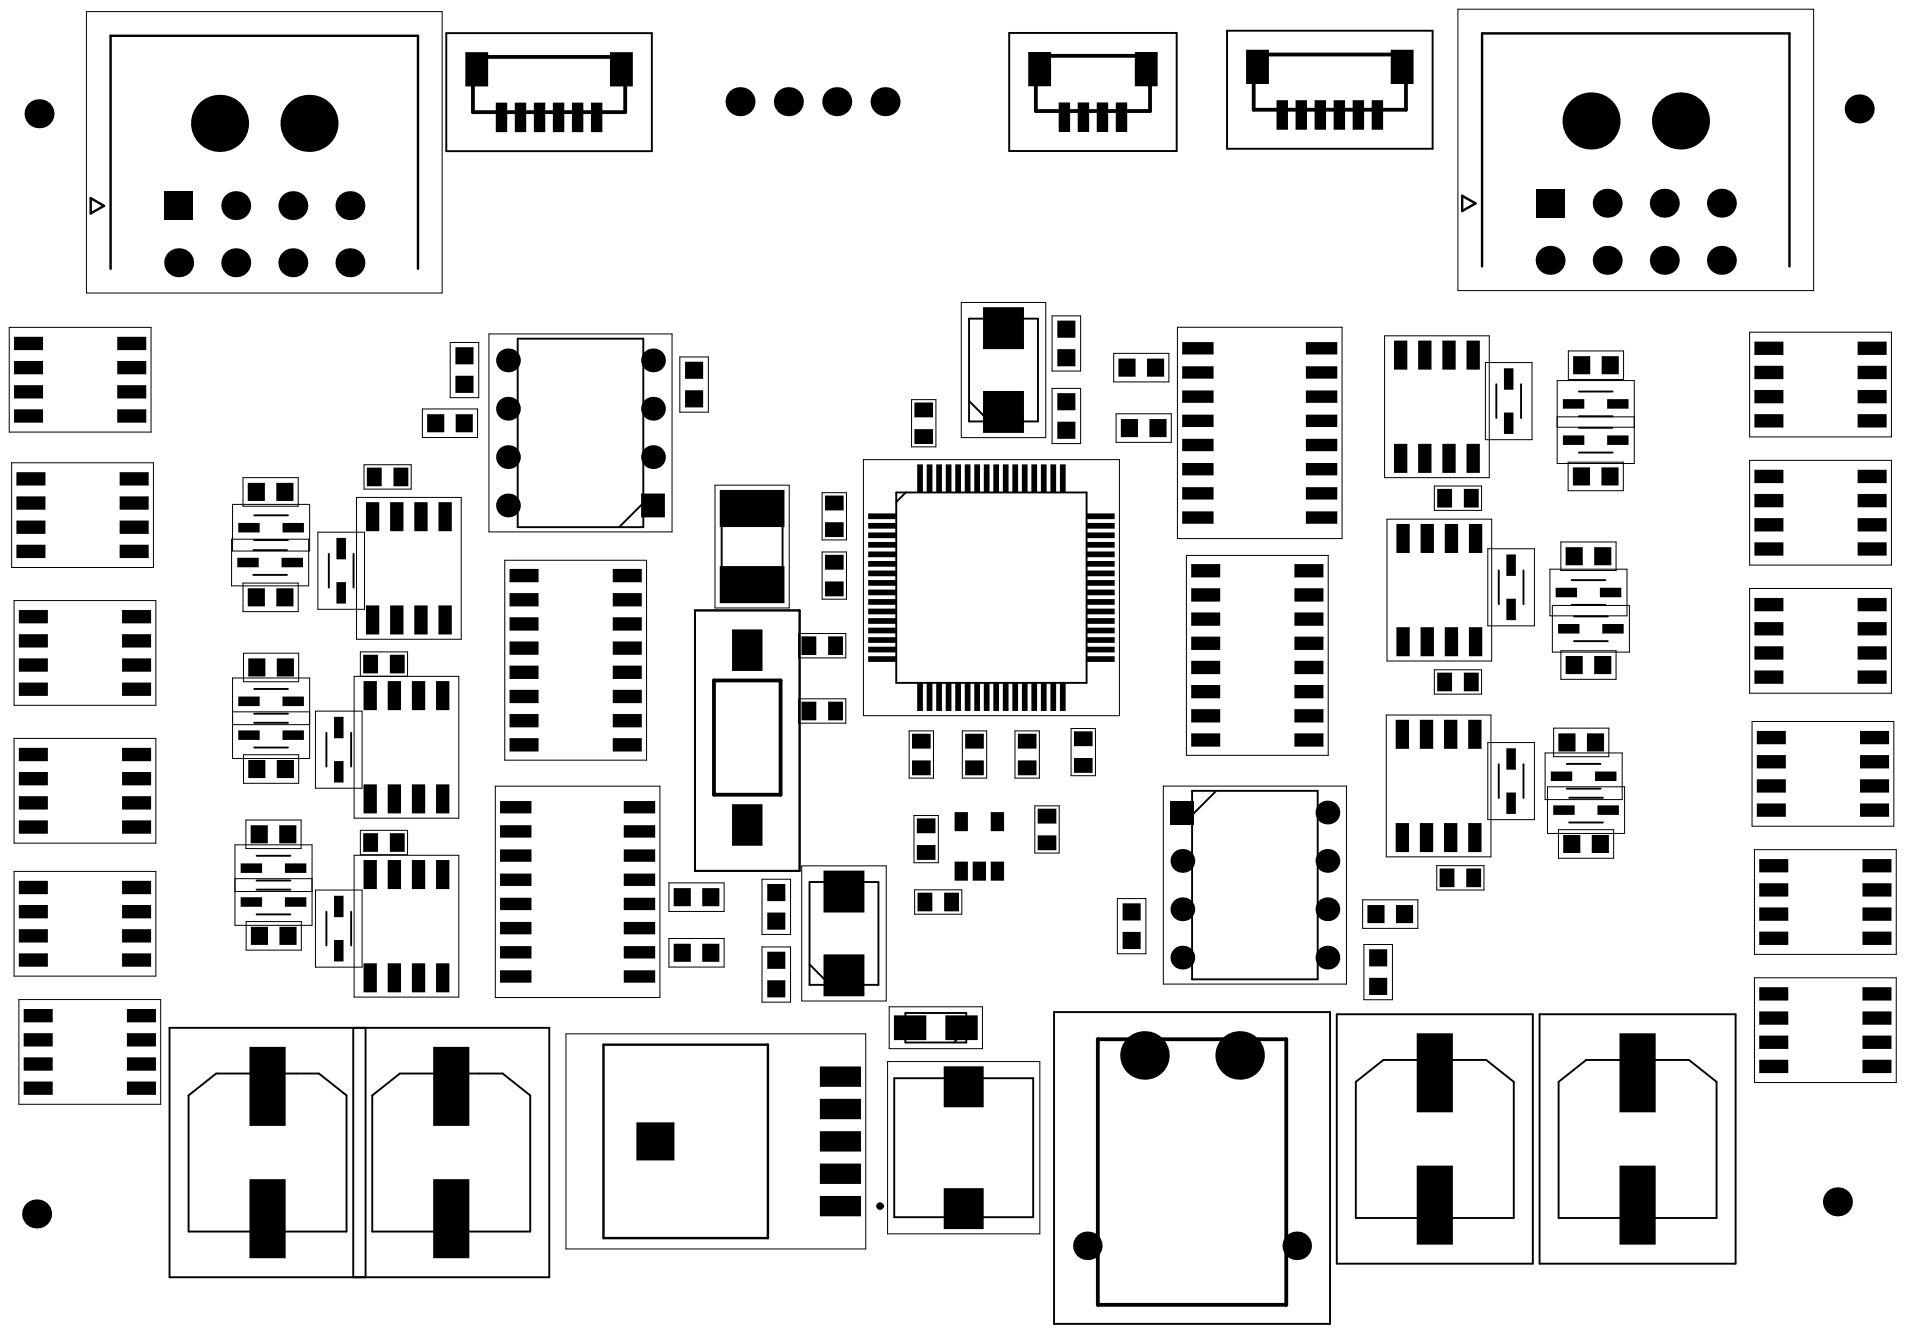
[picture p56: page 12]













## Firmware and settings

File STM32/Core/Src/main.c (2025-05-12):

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
/* Includes ------------------------------------------------------------------*/
#include "main.h"
#include "adc.h"
#include "dma.h"
#include "tim.h"
#include "usart.h"
#include "gpio.h"

/* USER CODE BEGIN Includes */
#include <stdbool.h>
#include <stdint.h>
#include <stdio.h>
#include <math.h>
#define NUM_SAMPLES 20

/* USER CODE END Includes */


/* USER CODE BEGIN PV */
typedef struct {
    float kp;
    float ki;
    float kd;
    float prev_error;
    float integral;
} PID_Controller;

// Структура состояния корректирующего устройства
typedef struct {
    float e1; // e[n-1]
    float e2; // e[n-2]
    float y1; // y[n-1]
    float y2; // y[n-2]
} CorrectorState;

// Структура коэффициентов корректирующего устройства
typedef struct {
    float b0, b1, b2;
    float a1, a2;
} CorrectorCoefficients;

// �?нициализация коэффициентов корректирующего устройства
static inline void Corrector_Init(CorrectorCoefficients *coeffs) {
    coeffs->b0 = 1811.0f;
    coeffs->b1 = -3529.0f;
    coeffs->b2 = 1719.0f;
    coeffs->a1 = -1.188f;
    coeffs->a2 = 0.1896f;
}


PID_Controller pid1 = {1.0f, 0.001f, 1.0f, 0, 0}; // Тюнинг подбирается экспериментально
PID_Controller pid2 = {11.5f, 0.004f, 3.7f, 0, 0};

volatile bool input_mode = false;
uint32_t adc_value_ch2 = 0;
volatile uint32_t adc_values[4] = {0,0,0,0};
float smooth_adc[4] = {0};
volatile uint32_t adc_raw_avg[4] = {0};  // усреднённые значения
volatile uint32_t last_button_press = 0;
float angle_pot1, angle_pot2;
float angle_enc1, angle_enc2;
volatile float sine_angle_2 = 90;
volatile float step_angle_2 = 90;
volatile float step_time = 0;
volatile float pwm1 = 0;
volatile float pwm2 = 0;
char uart_buf[50];
volatile float tim5_itr = 0;
volatile uint8_t busy = 0;

/* USER CODE END PV */

void SystemClock_Config(void);
/* USER CODE BEGIN 0 */

float GenerateSineValue(float freq_hz, float min_val, float max_val)
{
    static float time_ms = 0.0f;

    // Амплитуда и смещение
    float amplitude = (max_val - min_val) / 2.0f;
    float offset = (max_val + min_val) / 2.0f;

    // Вычисление значения
    float radians = 2.0f * M_PI * freq_hz * (time_ms / 1000.0f);
    float sine_value = offset + amplitude * sinf(radians);

    // Увеличение времени
    time_ms += 1.0f;
    if (time_ms >= 1000.0f / freq_hz) {
        time_ms -= 1000.0f / freq_hz;  // сброс по периоду
    }

    return sine_value;
}

float GenerateStepValue(float time, float min_val, float max_val)
{

    float step_value = min_val;

    if (step_time >= 0 && step_time <= time/2){
    	step_value = min_val;
    }
    else{
    	step_value = max_val;
    }

    // Увеличение времени
    step_time += 1.0f;
    if (step_time >= time) {
    	step_time = 0;
    }

    return step_value;
}



float PID_Compute(PID_Controller* pid, float setpoint, float measured)
{
    float error = setpoint - measured;

    pid->integral += error;
    float derivative = error - pid->prev_error;
    pid->prev_error = error;

    float output = pid->kp * error + pid->ki * pid->integral + pid->kd * derivative;



    return output;
}


// Ограничение значения в диапазоне [min, max]
static inline float Clamp(float value, float min, float max) {
    if (value > max) return max;
    if (value < min) return min;
    return value;
}

// Функция обновления корректирующего устройства
static inline int16_t Corrector_Update(CorrectorCoefficients *coeffs, CorrectorState *state, float target_angle, float current_angle) {
    float error = target_angle - current_angle;


    if (error > -0.5f && error < 0.5f) {
        return 0; // Игнорируем малую ошибку, PWM = 0
    }

    // Вычисление выхода
    float output = (coeffs->b0 * error)
                 + (coeffs->b1 * state->e1)
                 + (coeffs->b2 * state->e2)
                 - (coeffs->a1 * state->y1)
                 - (coeffs->a2 * state->y2);

    // Ограничение выхода
    output = Clamp(output, -839.0f, 839.0f);

    // Обновление состояния
    state->e2 = state->e1;
    state->e1 = error;
    state->y2 = state->y1;
    state->y1 = output;

    // Возврат значения в целочисленном формате для Ш�?М
    return (int16_t)output;
}


// Мотор 1: PWM на PB13, направление на PA9
void SetDirection1(bool cw)
{
	cw = !cw;
    HAL_GPIO_WritePin(GPIOA, GPIO_PIN_9, cw ? GPIO_PIN_SET : GPIO_PIN_RESET);
}

// Мотор 2: PWM на PB7, направление на PA10
void SetDirection2(bool cw)
{
    HAL_GPIO_WritePin(GPIOA, GPIO_PIN_10, cw ? GPIO_PIN_SET : GPIO_PIN_RESET);
}

// Установка Ш�?М — ожидается значение от 0 до 839
void PWM_Motor1(uint16_t pwm_value)
{
    if (pwm_value > 839) pwm_value = 839;
    __HAL_TIM_SET_COMPARE(&htim1, TIM_CHANNEL_1, pwm_value); // таймер для PB13
}

void PWM_Motor2(uint16_t pwm_value)
{
    if (pwm_value > 839) pwm_value = 839;
    __HAL_TIM_SET_COMPARE(&htim4, TIM_CHANNEL_2, pwm_value); // таймер для PB7
}


void ControlMotor1(float target_angle)
{
    pwm1 = PID_Compute(&pid1, target_angle, angle_enc2);


}

void ControlMotor2(float target_angle)
{
    pwm2 = PID_Compute(&pid2, target_angle, angle_enc1);


}



void FilterADC(volatile uint32_t adc_input[4])
{
    static uint32_t adc_sum[4] = {0};
    static uint8_t sample_count = 0;

    for (int i = 0; i < 4; i++) {
        adc_sum[i] += adc_input[i];
    }

    sample_count++;

    if (sample_count >= NUM_SAMPLES) {
        for (int i = 0; i < 4; i++) {
            adc_raw_avg[i] = adc_sum[i] / NUM_SAMPLES;
            adc_sum[i] = 0; // сброс суммы
        }
        sample_count = 0;
    }
}


// Вход: adc_values[0] – [3]
// Выход: 4 угла в градусах
void ConvertADCToAngles(uint32_t adc_values[4], float* angle_pot1, float* angle_pot2,
                        float* angle_enc1, float* angle_enc2)
{
    // ——— Энкодер 1: диапазон 3885 шагов ≈ 337°
    const uint16_t ENC1_ZERO_POS = 2970-15;
    const uint16_t ENC1_STEPS = 3835+15;
    const float ENC1_MAX_DEGREES = 337.0f;

    // ——— Энкодер 2: диапазон 2088 шагов ≈ 183°
    const uint16_t ENC2_ZERO_POS = 4060-15;
    const uint16_t ENC2_STEPS = 2088+15;
    const float ENC2_MAX_DEGREES = 183.0f;

    // ——— Энкодер 1
    uint32_t raw_enc1 = adc_values[2];
    int32_t diff1 = (int32_t)raw_enc1 - ENC1_ZERO_POS;
    if (diff1 < 0) diff1 += 4096;
    if (diff1 > ENC1_STEPS) diff1 = ENC1_STEPS;  // ограничим
    *angle_enc1 = ((float)diff1 / ENC1_STEPS) * ENC1_MAX_DEGREES;

    // ——— Энкодер 2
    uint32_t raw_enc2 = adc_values[3];
    int32_t diff2 = (int32_t)raw_enc2 - ENC2_ZERO_POS;
    if (diff2 < 0) diff2 += 4096;
    if (diff2 > ENC2_STEPS) diff2 = ENC2_STEPS;
    *angle_enc2 = ((float)diff2 / ENC2_STEPS) * ENC2_MAX_DEGREES;

    // ——— Потенциометры по масштабу энкодеров
    float angle_pot1_tmp = adc_values[0] * (ENC1_MAX_DEGREES / 4095.0f);
	float angle_pot2_tmp = adc_values[1] * (ENC2_MAX_DEGREES / 4095.0f);


    if (angle_pot1_tmp < 10.0f){
    	*angle_pot1 = 10.0f;
    }
    else if (angle_pot1_tmp > 330.0f){
    	*angle_pot1 = 330.0f;
    }
    else *angle_pot1 = angle_pot1_tmp;


    if (angle_pot2_tmp < 8.0f){
        	*angle_pot2 = 8.0f;
    }
    else if (angle_pot2_tmp > 179.0f){
        	*angle_pot2 = 179.0f;
    }
    else *angle_pot2 = angle_pot2_tmp;


}

void HAL_GPIO_EXTI_Callback(uint16_t GPIO_Pin)
{

	if (GPIO_Pin == GPIO_PIN_4)
	  {
	    uint32_t current_time = HAL_GetTick();

	    if (current_time - last_button_press > 200) // 100 мс защита от дребезга
	    {
	    	input_mode = !input_mode;
	      last_button_press = current_time;
	    }
	  }


}

void HAL_TIM_PeriodElapsedCallback(TIM_HandleTypeDef *htim)
{



    if (htim->Instance == TIM5) {
    	tim5_itr = tim5_itr + 1;
    	if (pwm1 >= 0) {
    	        SetDirection1(true);  // CW
    	    } else {
    	        SetDirection1(false); // CCW
    	        pwm1 = -pwm1;
    	    }

    	    if (pwm1 > 839.0f) pwm1 = 839.0f;
    	    PWM_Motor1((uint16_t)pwm1);

    	    if (pwm2 >= 0) {
    	            SetDirection2(true);  // CW
    	        } else {
    	            SetDirection2(false); // CCW
    	            pwm2 = -pwm2;
    	        }

    	        if (pwm2 > 839.0f) pwm2 = 839.0f;
    	        PWM_Motor2((uint16_t)pwm2);


    }

    if (htim->Instance == TIM3) {
        	sine_angle_2 = GenerateSineValue(9.0f, 20.0f, 180.0f);
        	step_angle_2 = GenerateStepValue(55.0f, 90.0f, 180.0f);
        }
}


float ReadAngleMotor2(void) {
    return angle_enc1;
}

void CommandMotor2(float pwm) {
    if (pwm >= 0) {
        SetDirection2(true);
    } else {
        SetDirection2(false);
        pwm = -pwm;
    }
    PWM_Motor2((uint16_t)pwm);
}


void send_data(float v1, float v2) {
    int len = snprintf(uart_buf, sizeof(uart_buf), "%.3f,%.3f\r\n", v1, v2);
    HAL_UART_Transmit(&huart6, (uint8_t*)uart_buf, len, HAL_MAX_DELAY);
}

void send_data_non_blocking(float v1, float v2) {
    static char buf[50];

    if (!busy) {
        int len = snprintf(buf, sizeof(buf), "%.2f,%.2f\r\n", v1, v2);
        if (HAL_UART_Transmit_IT(&huart6, (uint8_t*)buf, len) == HAL_OK) {
            busy = 1;
        }
    }
}

// В прерывании окончания передачи:
void HAL_UART_TxCpltCallback(UART_HandleTypeDef *huart) {
    if (huart->Instance == USART6) {
        busy = 0;
    }
}

/* USER CODE END 0 */

/**
  * @brief  The application entry point.
  * @retval int
  */
int main(void)
{
  /* MCU Configuration--------------------------------------------------------*/

  /* Reset of all peripherals, Initializes the Flash interface and the Systick. */
  HAL_Init();

  /* Configure the system clock */
  SystemClock_Config();

  /* Initialize all configured peripherals */
  MX_GPIO_Init();
  MX_DMA_Init();
  MX_ADC1_Init();
  MX_TIM1_Init();
  MX_TIM4_Init();
  MX_TIM3_Init();
  MX_USART6_UART_Init();
  MX_TIM5_Init();
  /* USER CODE BEGIN 2 */
  HAL_TIM_PWM_Start(&htim4, TIM_CHANNEL_2);
  HAL_TIMEx_PWMN_Start(&htim1, TIM_CHANNEL_1);
  HAL_ADC_Start_DMA(&hadc1, (uint32_t*)adc_values, 4);
  __HAL_TIM_SET_COMPARE(&htim4, TIM_CHANNEL_2, 0);
  __HAL_TIM_SET_COMPARE(&htim1, TIM_CHANNEL_1, 0);
  HAL_TIM_Base_Start_IT(&htim3);
  HAL_TIM_Base_Start_IT(&htim5);

  CorrectorState corrector_state1 = {0};
  CorrectorState corrector_state2 = {0};
  CorrectorCoefficients corrector_coeffs;

  Corrector_Init(&corrector_coeffs);

  //FilterADC(adc_values);
  //ConvertADCToAngles(adc_raw_avg, &angle_pot1, &angle_pot2, &angle_enc1, &angle_enc2);
  //AutoTunePID(&pid2, ReadAngleMotor2, CommandMotor2);
  /* USER CODE END 2 */

  /* Infinite loop */
  /* USER CODE BEGIN WHILE */
  while (1)
  {
    /* USER CODE END WHILE */

    /* USER CODE BEGIN 3 */
	  FilterADC(adc_values);
	  ConvertADCToAngles(adc_raw_avg, &angle_pot1, &angle_pot2, &angle_enc1, &angle_enc2);


	  if (input_mode) // Если true то используем потенциометры для управления
	      {
	        HAL_GPIO_WritePin(GPIOB, GPIO_PIN_12, GPIO_PIN_SET);   // Включить LED PB12
	        HAL_GPIO_WritePin(GPIOA, GPIO_PIN_15, GPIO_PIN_RESET);  // Выключить LED PB3
	        //ControlMotor2(angle_pot1);
	        //ControlMotor1(angle_pot2);
	        pwm2 = Corrector_Update(&corrector_coeffs, &corrector_state2, angle_pot1, angle_enc1);
	        pwm1 = Corrector_Update(&corrector_coeffs, &corrector_state1, sine_angle_2, angle_enc1);
	        //send_data_non_blocking(sine_angle_2, angle_enc1);
	        //PWM_Motor2(500);
	        //SetDirection2(false); //против часовой

	      }
	      else // Если false то используем заготовленный сигнал sin
	      {
	        HAL_GPIO_WritePin(GPIOB, GPIO_PIN_12, GPIO_PIN_RESET); // Выключить LED PB12
	        HAL_GPIO_WritePin(GPIOA, GPIO_PIN_15, GPIO_PIN_SET);    // Включить LED PB3
	        ControlMotor2(step_angle_2);
	        //pwm2 = Corrector_Update(&corrector_coeffs, &corrector_state2, sine_angle_2, angle_enc1);
	        //ControlMotor2(sine_angle_2);
	        send_data_non_blocking(step_angle_2, angle_enc1);
	        //PWM_Motor2(500);
	        //SetDirection2(true);
	      }


  }
  /* USER CODE END 3 */
}

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


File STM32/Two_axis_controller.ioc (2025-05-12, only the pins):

Mcu.UserName=STM32F401CCUx
PA0-WKUP.Signal=SYS_WKUP
PA1.Signal=ADCx_IN1
PA10.Signal=GPIO_Output
PA11.Signal=USART6_TX
PA12.Signal=USART6_RX
PA13.Signal=SYS_JTMS-SWDIO
PA14.Signal=SYS_JTCK-SWCLK
PA15.Signal=GPIO_Output
PA2.Signal=ADCx_IN2
PA3.Signal=ADCx_IN3
PA4.Signal=ADCx_IN4
PA9.Signal=GPIO_Output
PB12.Signal=GPIO_Output
PB13.Signal=TIM1_CH1N
PB3.Signal=SYS_JTDO-SWO
PB4.Signal=GPXTI4
PB7.Signal=S_TIM4_CH2
PC13-ANTI_TAMP.Signal=GPIO_Output
PC14-OSC32_IN.Signal=RCC_OSC32_IN
PC15-OSC32_OUT.Signal=RCC_OSC32_OUT

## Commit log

2024-09-23 Оформление исследовательской части
2024-09-23 создание структуры
2024-10-01 исправление идеологии
2024-10-02 некоторые изменения после консультации
2024-10-21 Кинематическая схема
2024-10-22 Кинематическая схема новый текст и функц схема
2024-10-22 Кинематическая схема новый текст +++
2024-11-07 приведение к ГОСТУ
2024-11-27 Выбран двигатель
    [Антенна.ipt, Грубая сборка.iam, Грубый_макет.0001.ipt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]
2024-11-29 Нир 1.0 готов предфинальная версия
2024-12-04 Исправления НИР, создание проекта в matlab, моделирование bldc и редуктора
2024-12-10 Полная модель линейная
2024-12-23 Финальная версия КП по тау и моделей в матлабе
    [Dual_BLDC_Controller.PrjPcb, PCB_board.PcbDoc, Схема_принципиальная_JY01.SchDoc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]
2024-12-26 НИР и ТАУ 100% электроника в работе
    [Схема_принципиальная_общая.SchDoc]
2025-01-10 Доделал принципиальные схемы 1.0
    [Схема_принципиальная_JY01.SchDoc, Схема_принципиальная_общая.SchDoc]
2025-01-19 1.0 со всей документацией
    [Dual_BLDC_Controller.PrjPcb, PCB_board.DWG, Схема_принципиальная_JY01.SchDoc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]
2025-01-21 некоторые исправления ошибок
    [Dual_BLDC_Controller.PrjPcb]
2025-01-23 Исправлены ошибки после защиты, сама плата еще требует доработки
    [Схема_принципиальная_JY01.SchDoc]
2025-04-07 Курсач по экономике
2025-04-09 Конструкторская часть
    [BLDC_3626.0003.ipt, BLDC_3626.ipt, GT2 40T 8 Bore v2.0001.iam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]
2025-04-16 программная часть
    [0402 Capacitor_001.ipt, 0402 Capacitor_002.ipt, 0402 Capacitor_003.ipt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]
2025-04-29 Алгоритмы поиска и слежения и первая версия нир2
    [Вал 2 оси.stp, Вал вертикальной оси.stp, Верх редуктора.0003.ipt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]
2025-05-12 Некоторые изменения в НИР2 и новые испытания
2025-05-12 Уборка

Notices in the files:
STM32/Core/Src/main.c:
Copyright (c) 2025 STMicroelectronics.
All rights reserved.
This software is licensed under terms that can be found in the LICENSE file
